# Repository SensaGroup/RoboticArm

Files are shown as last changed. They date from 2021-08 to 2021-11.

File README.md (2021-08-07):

# SENSA - Robotic Arm 

Genral repository for files pertaining to the robotic arm that is part of SENSA GROUP education.  

## Description
The PCB interfaces the microcontroller with 5 stepper drivers and 5 encoders. 

## Features
- Main controller: ESP32WROOM-U.
- Wifi.
- Bluetooth.
- Programming over USB C. 
- 2x TB6600 Drivers. 
- 3x pinouts for general stepstick drivers. 
- 5x AMT102 encoder inputs. 
- Software (TBD)

## Pictures
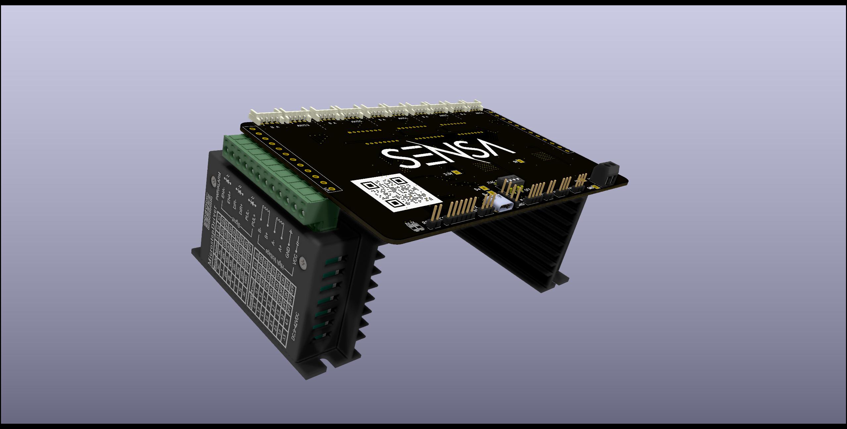
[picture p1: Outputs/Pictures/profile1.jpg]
Top_view


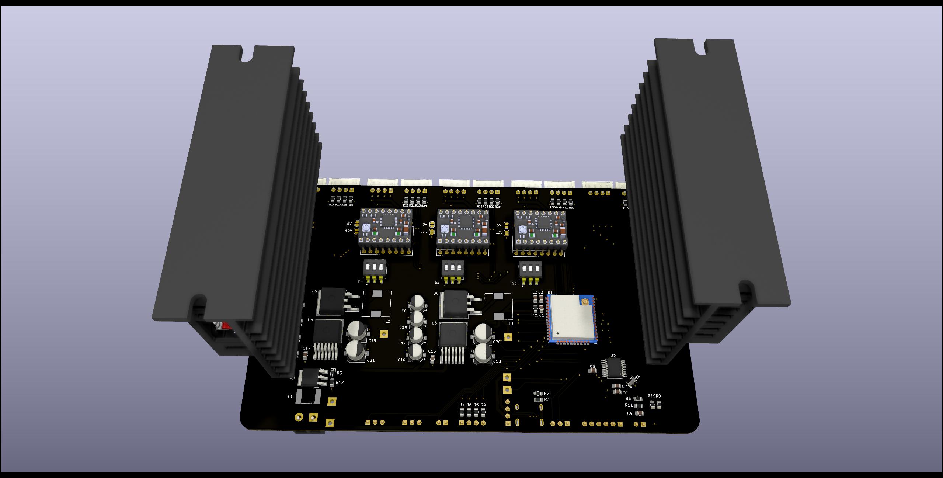
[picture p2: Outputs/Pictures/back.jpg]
Back_view


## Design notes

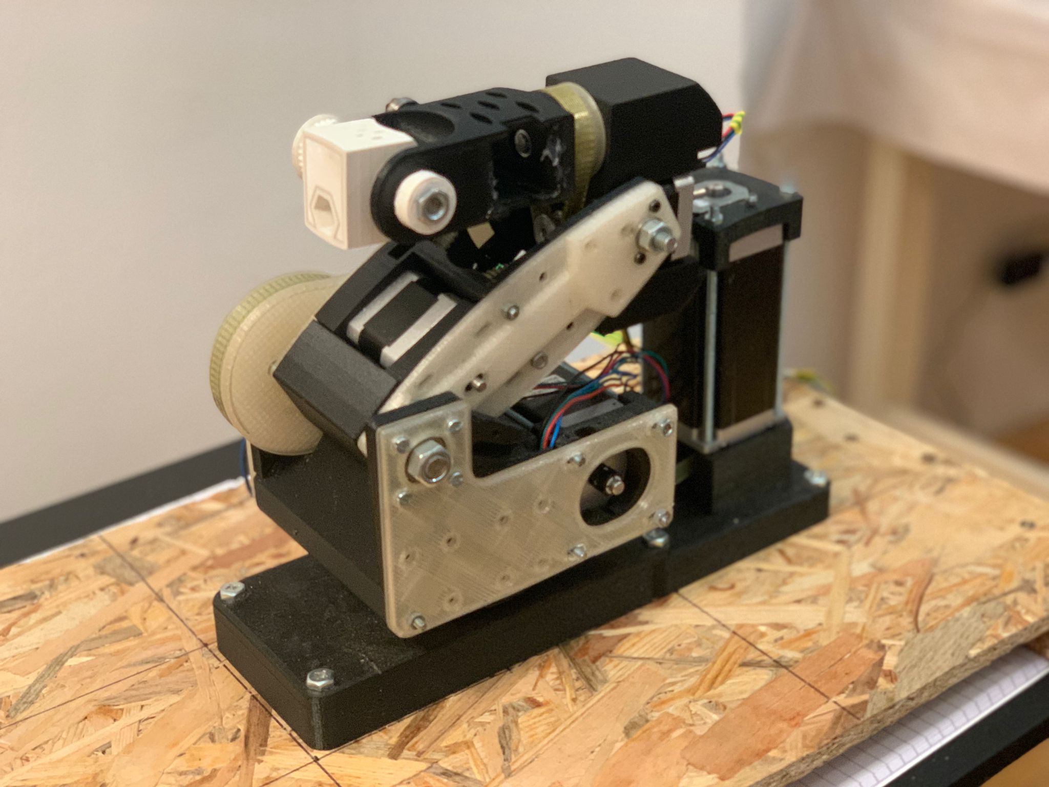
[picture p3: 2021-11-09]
Documents/Slika2.jpeg

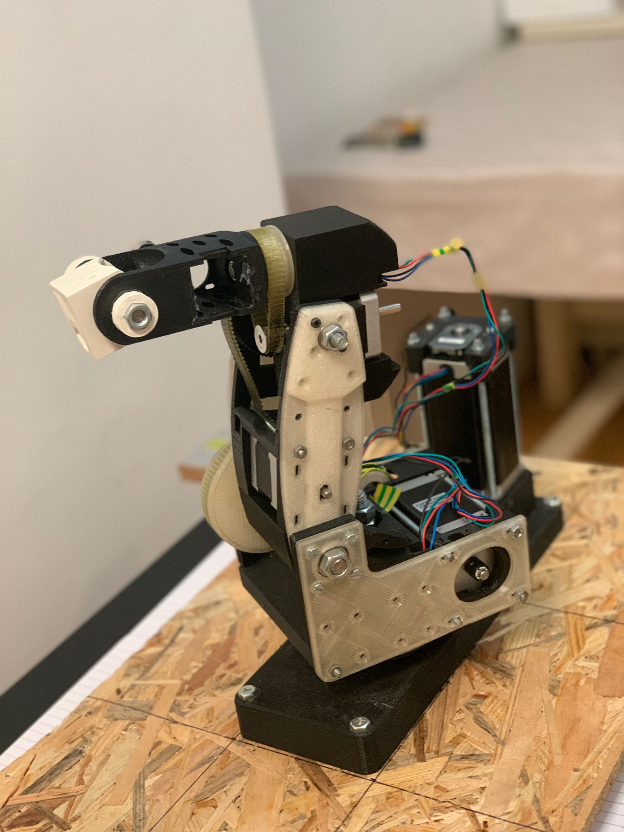
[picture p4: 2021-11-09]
Documents/Slika1.jpeg

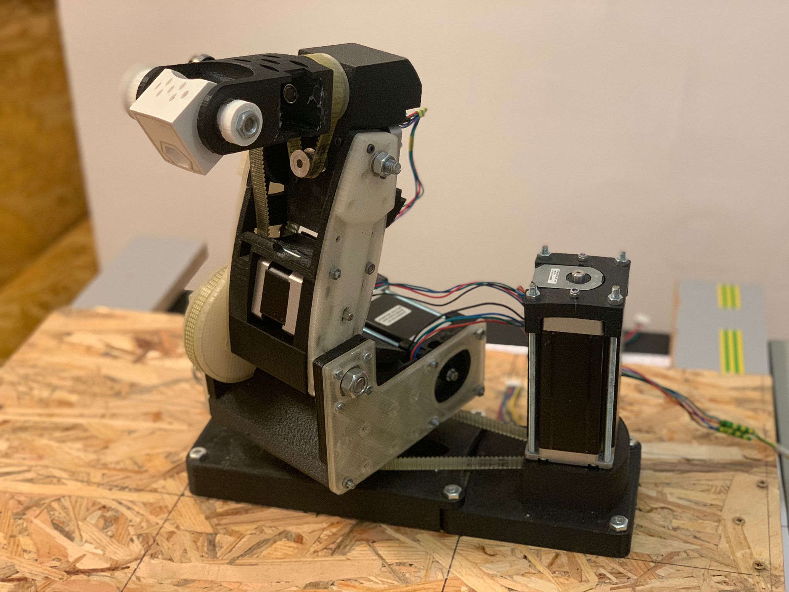
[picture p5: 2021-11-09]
Documents/Slika3.jpeg

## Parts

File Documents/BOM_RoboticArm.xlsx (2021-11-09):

PART | PIECES | PRICE | DISTR. | LINK
ESP32-WROOM-32U (16MB) | 2 | 7.83 | DIGI KEY | https://www.digikey.com/en/products/detail/espressif-systems/ESP32-WROOM-32U-16MB/9381721
AMT102-V | 5 | 100.53 | DIGI KEY | https://www.digikey.com/en/products/detail/cui-devices/AMT102-V/827015
LM2678S-5.0/NOPB | 2 | 11.78 | DIGI KEY | https://www.digikey.com/en/products/detail/texas-instruments/LM2678S-5-0-NOPB/363825
LM2678SX-3.3/NOPB | 2 | 10.95 | DIGI KEY | https://www.digikey.com/en/products/detail/texas-instruments/LM2678SX-3-3-NOPB/366920
ANTX100P011B24003 | 2 | 2.57 | DIGI KEY | https://www.digikey.com/en/products/detail/yageo/ANTX100P011B24003/9360397
ATP106-TL-H | 1 | 0.82 | DIGI KEY | https://www.digikey.com/en/products/detail/on-semiconductor/ATP106-TL-H/2165409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
ASMDC300F/24-2 | 1 | 0.76 | DIGI KEY | https://www.digikey.com/en/products/detail/littelfuse-inc/ASMDC300F-24-2/6623875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
STPS8H100G-TR | 1 | 0.83 | DIGI KEY | https://www.digikey.com/en/products/detail/stmicroelectronics/STPS8H100G-TR/1039718
NP36P06SLG-E1-AY | 1 | 1.26 | DIGI KEY | https://www.digikey.com/en/products/detail/renesas-electronics-america-inc/NP36P06SLG-E1-AY/2764260
ETQ-P4M220KVC | 1 | 0.98 | DIGI KEY | https://www.digikey.com/en/products/detail/panasonic-electronic-components/ETQ-P4M220KVC/6134801
1054500101 | 2 | 3.69 | DIGI KEY | https://www.digikey.com/en/products/detail/molex/1054500101/5843890
MCP2200-I/SS | 2 | 5.94 | FARNELL | https://export.farnell.com/microchip/mcp2200-i-ss/ic-usb2-0-to-uart-w-gpio-20ssop/dp/1781149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
AWSCR-12.00CELB-C33-T3 | 2 | 0.93 | DIGI KEY | https://www.digikey.com/en/products/detail/abracon-llc/AWSCR-12-00CELB-C33-T3/10232536
156120VS75000 | 20 | 3.03 | DIGI KEY | https://www.digikey.com/en/products/detail/w%C3%BCrth-elektronik/156120VS75000/4490062
10081121 | 10 | 14.66 | DIGI KEY | https://www.digikey.com/en/products/detail/molex/0010081121/3072144?s=N4IgTCBcDaIIwAYEA45zHEBdAvkA
S4B-XH-A-1(LF)(SN) | 100 | 15.28 | DIGI KEY | https://www.digikey.com/en/products/detail/jst-sales-america-inc/S4B-XH-A-1-LF-SN/9961923
XHP-4 | 100 | 5.12 | DIGI KEY | https://www.digikey.com/en/products/detail/jst-sales-america-inc/XHP-4/683353
SXH-002T-P0.6 | 500 | 11.62 | DIGI KEY | https://www.digikey.com/en/products/detail/jst-sales-america-inc/SXH-002T-P0-6/1651063
1718560003 | 50 | 13.65 | DIGI KEY | https://www.digikey.com/en/products/detail/molex/1718560003/4423110
DS04-254-2-03BK-SMT | 10 | 4.39 | DIGI KEY | https://www.digikey.com/en/products/detail/cui-devices/DS04-254-2-03BK-SMT/11310920
09200-71-BDGB00 | 50 | 1.6 | DIGI KEY | https://www.digikey.com/en/products/detail/metz-connect-usa-inc/09200-71-BDGB00/13536314
DS04-254-2-04BK-SMT | 10 | 4.95 | DIGI KEY | https://www.digikey.com/en/products/detail/cui-devices/DS04-254-2-04BK-SMT/11310827
 |  |  | SIMPLE:
CRGCQ0805J100R | 100 | 1.47 | DIGI KEY | https://www.digikey.com/en/products/detail/te-connectivity-passive-product/CRGCQ0805J100R/8576730
LMK212BJ106MG-T | 10 | 1.24 | DIGI KEY | https://www.digikey.com/en/products/detail/taiyo-yuden/LMK212BJ106MG-T/1171629
CC0805ZRY5V9BB104 | 10 | 0.59 | DIGI KEY | https://www.digikey.com/en/products/detail/yageo/CC0805ZRY5V9BB104/2103099
C0805C474K5RECAUTO | 10 | 1.56 | DIGI KEY | https://www.digikey.com/en/products/detail/kemet/C0805C474K5RECAUTO/8646710
865080449011 | 10 | 3.95 | DIGI KEY | https://www.digikey.com/en/products/detail/w%C3%BCrth-elektronik/865080449011/5728034
C0805C103K1RAC7210 | 10 | 0.52 | DIGI KEY | https://www.digikey.com/en/products/detail/kemet/C0805C103K1RAC7210/8572452
865080645009 | 10 | 2.61 | DIGI KEY | https://www.digikey.com/en/products/detail/w%C3%BCrth-elektronik/865080645009/5728049
865080442003 | 20 | 3.2 | DIGI KEY | https://www.digikey.com/en/products/detail/w%C3%BCrth-elektronik/865080442003/5728026
ESR10EZPJ102 | 10 | 0.69 | DIGI KEY | https://www.digikey.com/en/products/detail/rohm-semiconductor/ESR10EZPJ102/1762748
RMCF0805JT5K10 | 10 | 0.17 | DIGI KEY | https://www.digikey.com/en/products/detail/stackpole-electronics-inc/RMCF0805JT5K10/1757930
RNCF0805DTE470R | 10 | 0.92 | DIGI KEY | https://www.digikey.com/en/products/detail/stackpole-electronics-inc/RNCF0805DTE470R/6241768
CRCW080510K0FKEAC | 10 | 0.53 | DIGI KEY | https://www.digikey.com/en/products/detail/vishay-dale/CRCW080510K0FKEAC/7928398
RMCF0805FT2K00 | 100 | 0.92 | DIGI KEY | https://www.digikey.com/en/products/detail/stackpole-electronics-inc/RMCF0805FT2K00/1760249
CRCW08053K90FKTA | 20 | 2.13 | DIGI KEY | https://www.digikey.com/en/products/detail/vishay-dale/CRCW08053K90FKTA/1222880
 | TOTAL: | 243.67

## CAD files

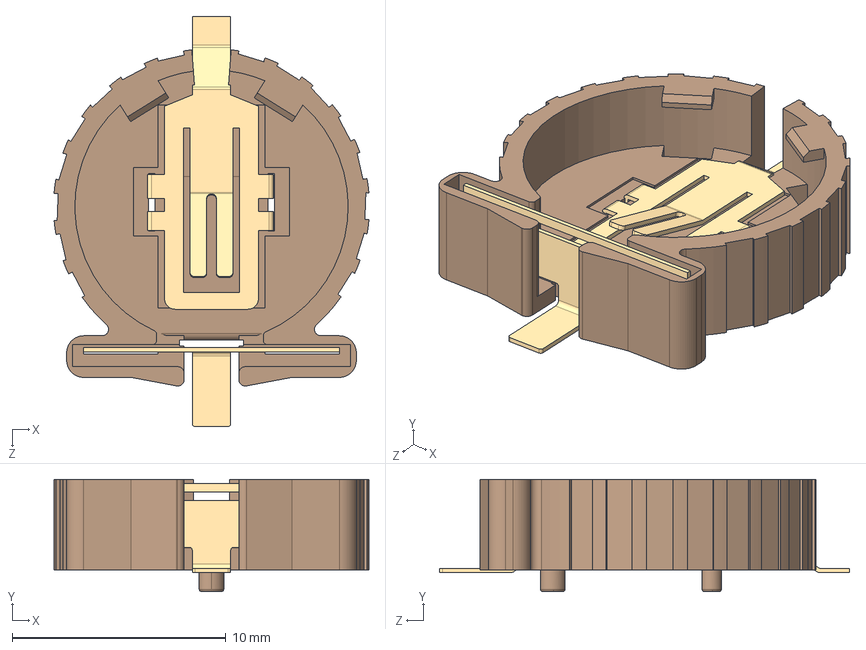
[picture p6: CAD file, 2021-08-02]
Arm_Mainboard/AddOns/3D/User Library-s8411-45r_asm.STEP
14.7 x 5.25 x 19.2 mm
S841-HOLDER
S841-LOWER-CONTACT
S841-REAR-CONTACT

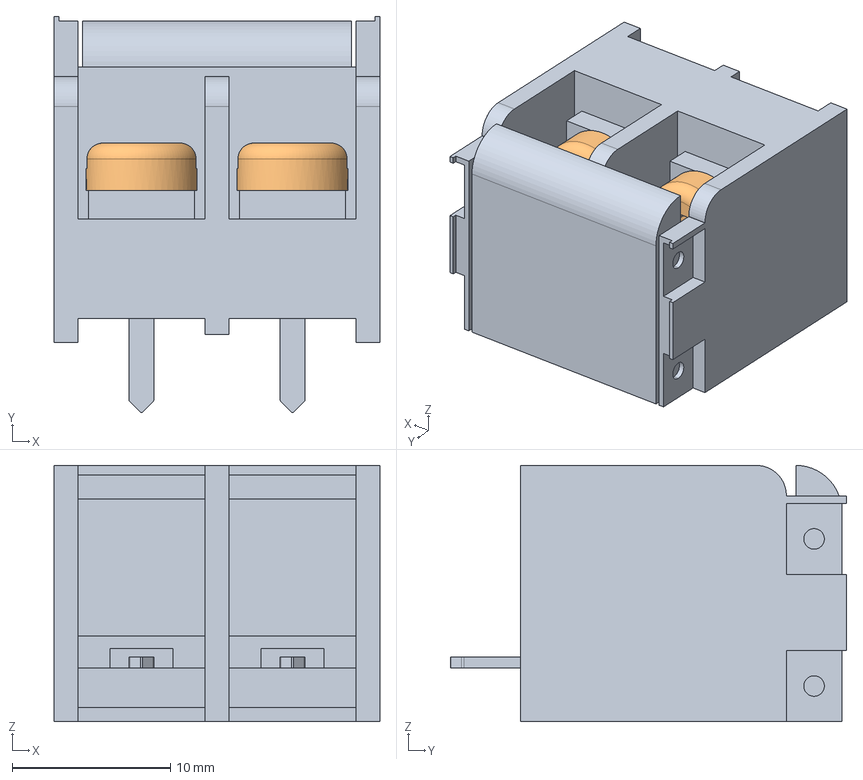
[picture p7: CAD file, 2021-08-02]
Arm_Mainboard/AddOns/3D/hb9500_asm.stp
20.6 x 25.0 x 16.2 mm
HB9500-1
M5X6 x 2

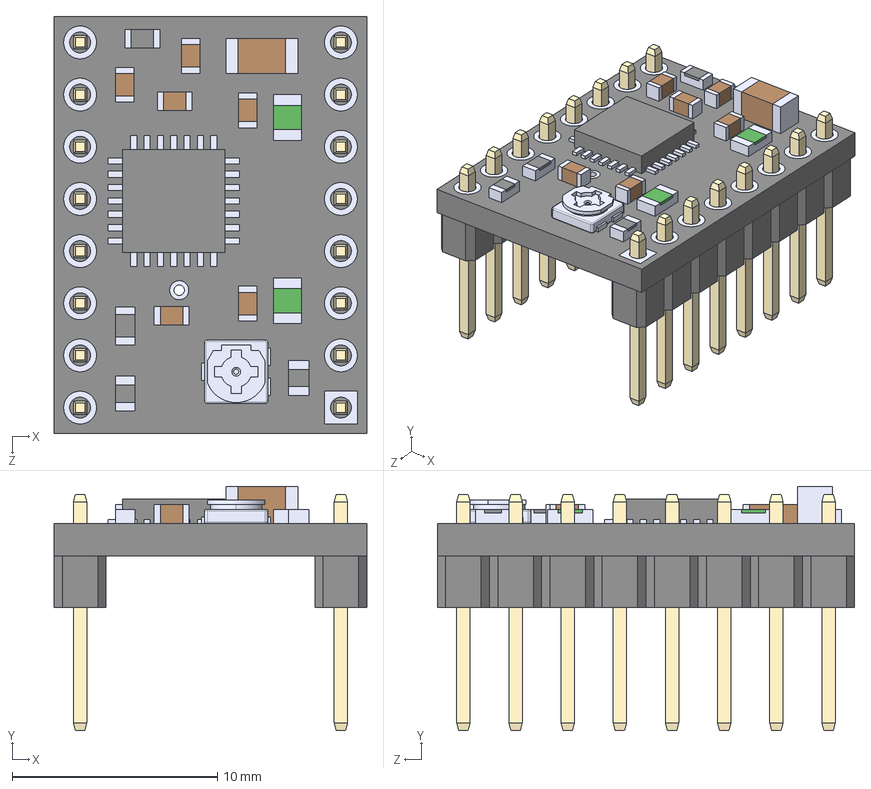
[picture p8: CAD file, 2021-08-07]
Arm_Mainboard/AddOns/3D/A4988 STEPPER MOTOR DRIVER CARRIER--3DModel-STEP-56544.STEP
15.2 x 11.9 x 20.3 mm

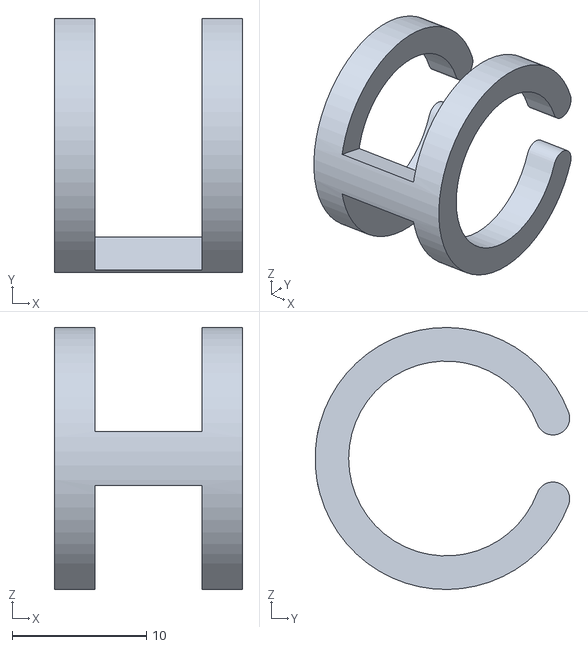
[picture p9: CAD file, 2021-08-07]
For 3D printing/Axis4limit.STL
14.0 x 18.9 x 19.5

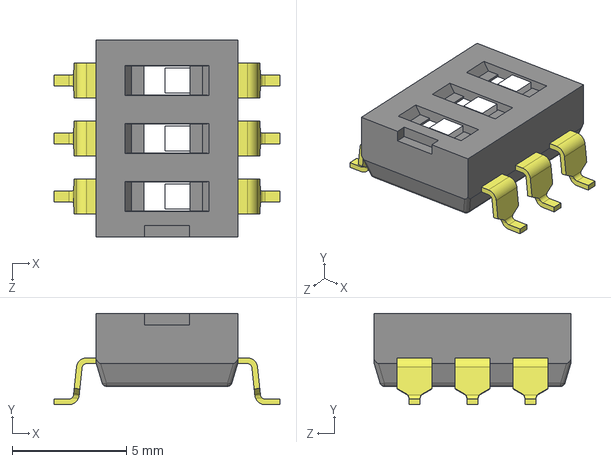
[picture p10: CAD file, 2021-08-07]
Arm_Mainboard/AddOns/3D/CUI_DEVICES_DS04-254-2-03BK-SMT.step
9.90 x 4.00 x 8.62 mm

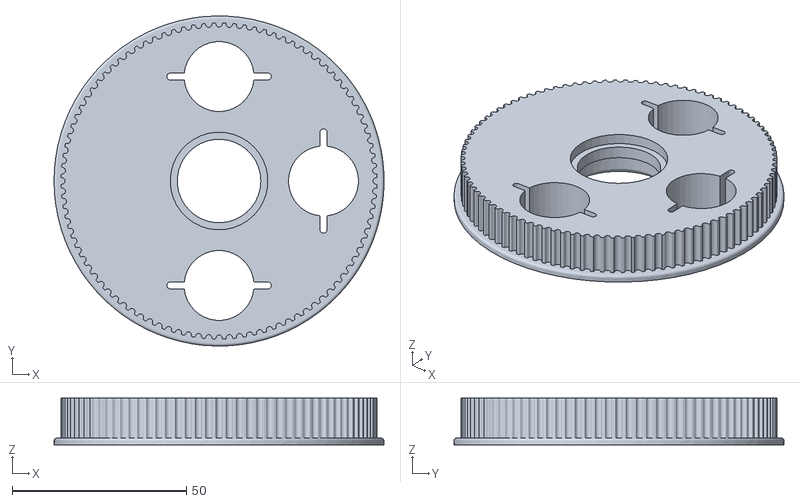
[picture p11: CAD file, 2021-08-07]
For 3D printing/Axis1Pulley_1.STL
94.8 x 94.8 x 13.5

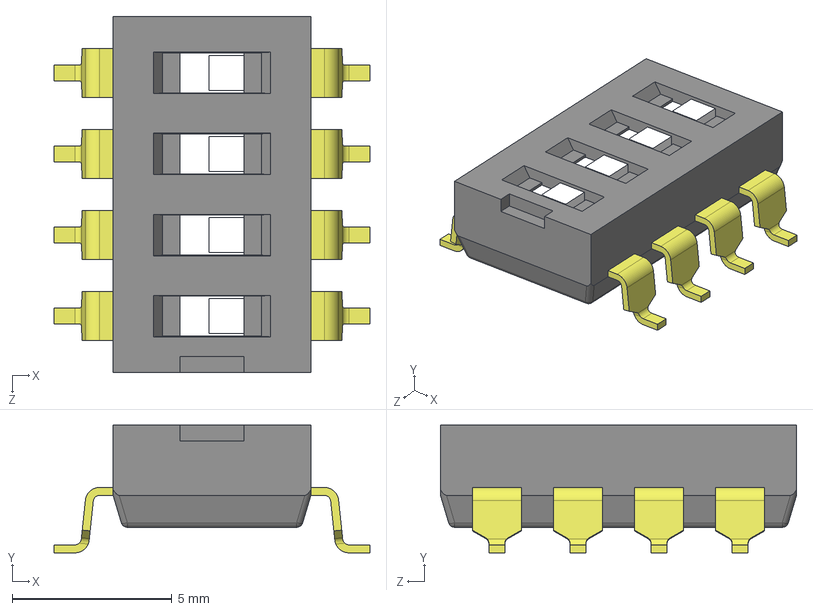
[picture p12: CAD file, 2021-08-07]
Arm_Mainboard/AddOns/3D/CUI_DEVICES_DS04-254-2-04BK-SMT.step
9.90 x 4.00 x 11.2 mm

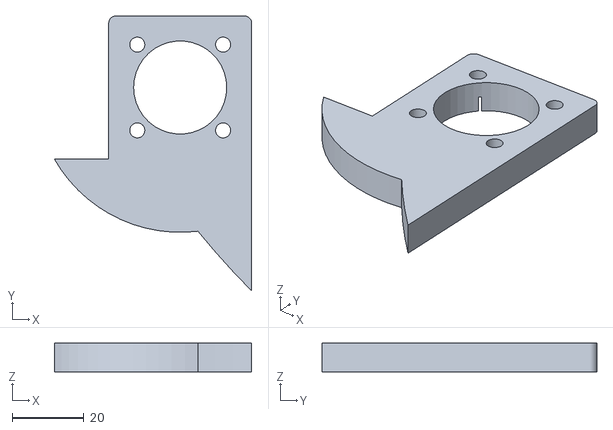
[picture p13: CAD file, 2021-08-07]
For 3D printing/Axis2bearingHolder_1.STL
55.2 x 76.9 x 8.00

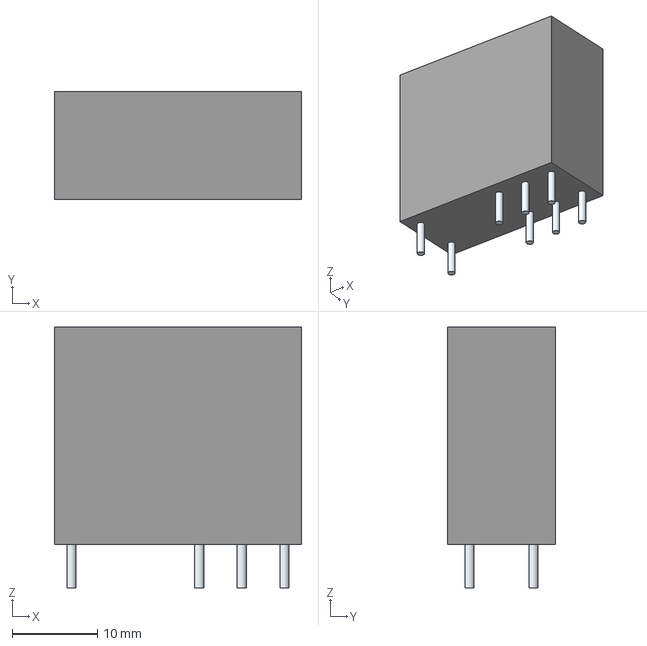
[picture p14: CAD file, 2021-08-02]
Arm_Mainboard/AddOns/3D/G2R-2-DC12.stp
29.0 x 12.7 x 30.6 mm
Leads x 8

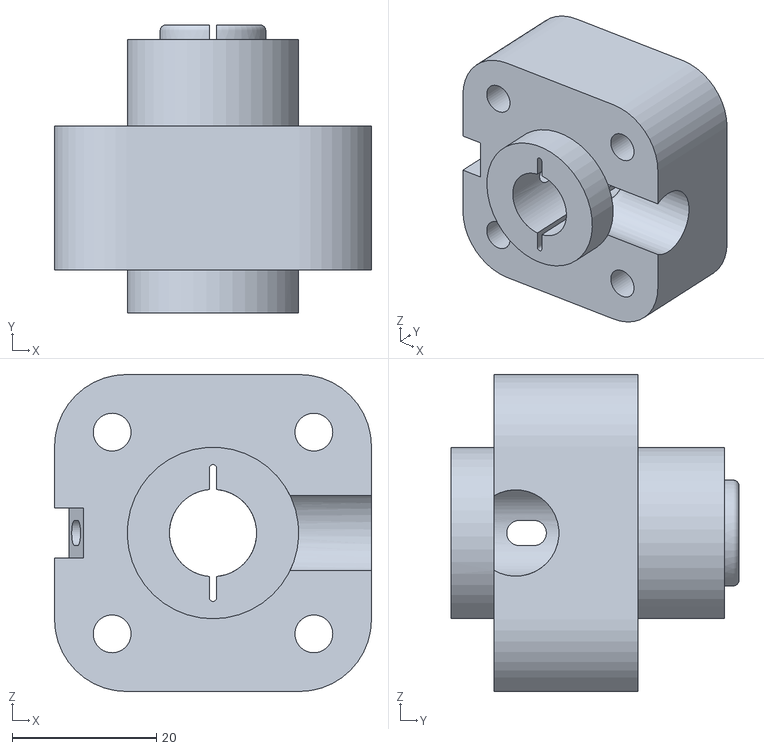
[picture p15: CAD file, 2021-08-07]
For 3D printing/Axis1Holder.STL
44.0 x 40.0 x 44.0

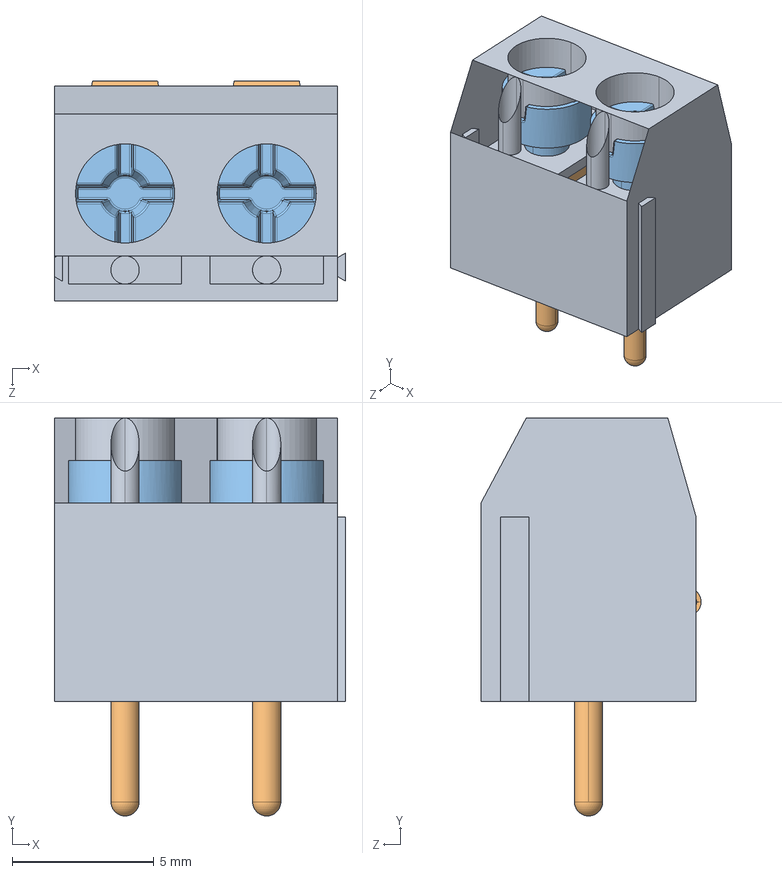
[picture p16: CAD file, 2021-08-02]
Arm_Mainboard/AddOns/3D/2 pins.STEP
10.3 x 14.1 x 7.77 mm
terminal_2 pins
Inner x 2
Screw x 2

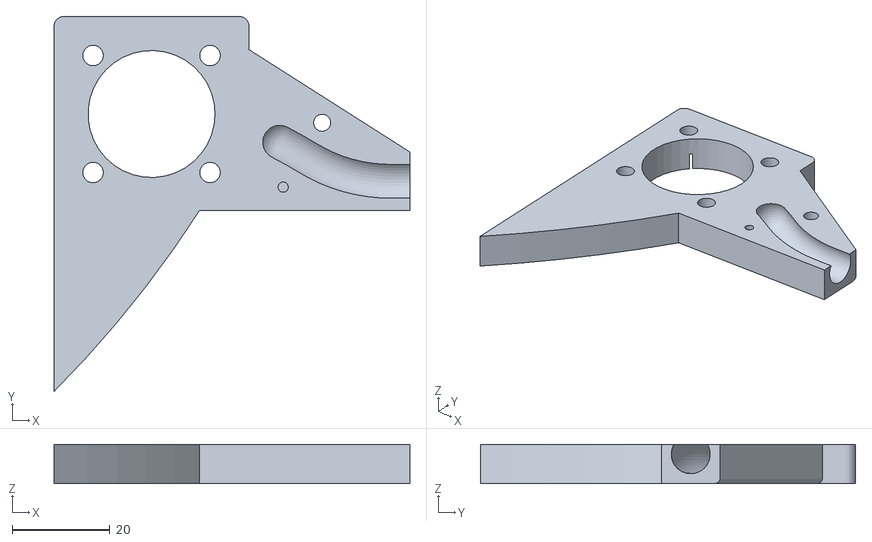
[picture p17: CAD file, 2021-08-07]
For 3D printing/Axis2bearingHolder.STL
73.0 x 76.9 x 8.00

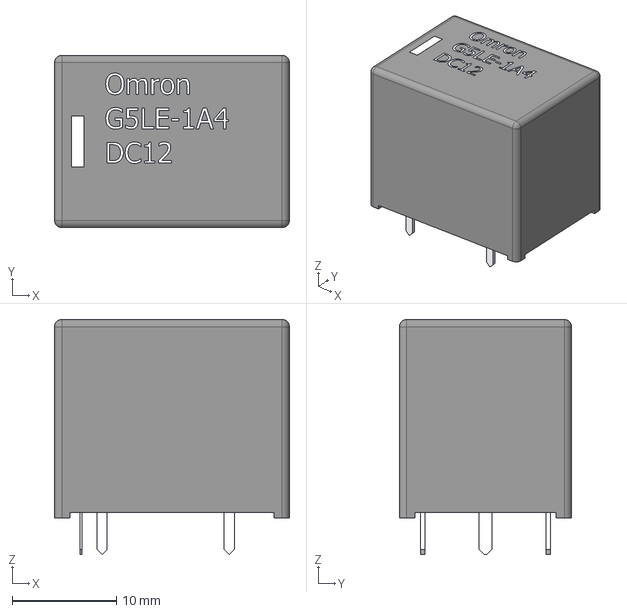
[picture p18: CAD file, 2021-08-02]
Arm_Mainboard/AddOns/3D/Omron_-_G5LE-1A4_DC12.step
22.5 x 16.5 x 22.5 mm

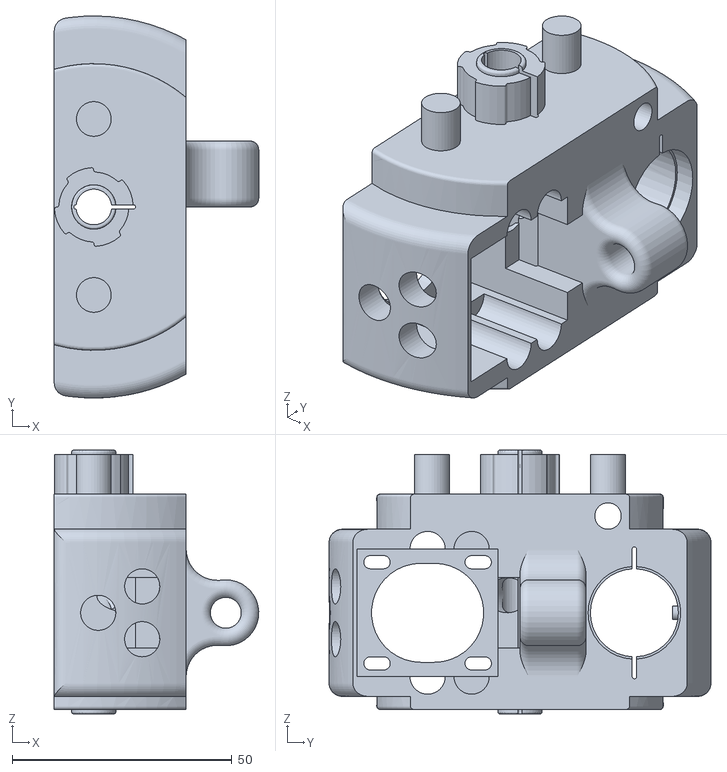
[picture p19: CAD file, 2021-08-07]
For 3D printing/Axis4.STL
46.5 x 86.8 x 60.0

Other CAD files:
Arm_Mainboard/AddOns/3D/MBS6_RCG.stp
For 3D printing/Axis1MotorHolderOp.STL
Arm_Mainboard/AddOns/3D/4 pins.STEP
For 3D printing/Axis3cover2.STL
Arm_Mainboard/AddOns/3D/1 pins.STEP
Arm_Mainboard/AddOns/3D/105450-0101.step
Arm_Mainboard/AddOns/3D/3 pins.STEP
Arm_Mainboard/AddOns/3D/577202B00000G.STEP
Arm_Mainboard/AddOns/3D/74HCT1G04GV,125.stp
Arm_Mainboard/AddOns/3D/AGQ200A24Z.stp
Arm_Mainboard/AddOns/3D/CSD19534Q5AT.STEP
Arm_Mainboard/AddOns/3D/DMP3007SFG-7.stp
Arm_Mainboard/AddOns/3D/S8411-45R--3DModel-STEP-56544.STEP
Arm_Mainboard/AddOns/3D/User Library-TB2.STEP
Arm_Mainboard/AddOns/3D/relay_omron_G5Q.STEP
For 3D printing/Axis1MotorHolder.STL
For 3D printing/Axis1washer.STL
For 3D printing/Axis2MotorOp.STL
For 3D printing/Axis2Pulley_1.STL
For 3D printing/Axis2part2.STL
For 3D printing/Axis3cover1.STL
For 3D printing/Axis3part3.STL
For 3D printing/Axis5.STL
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

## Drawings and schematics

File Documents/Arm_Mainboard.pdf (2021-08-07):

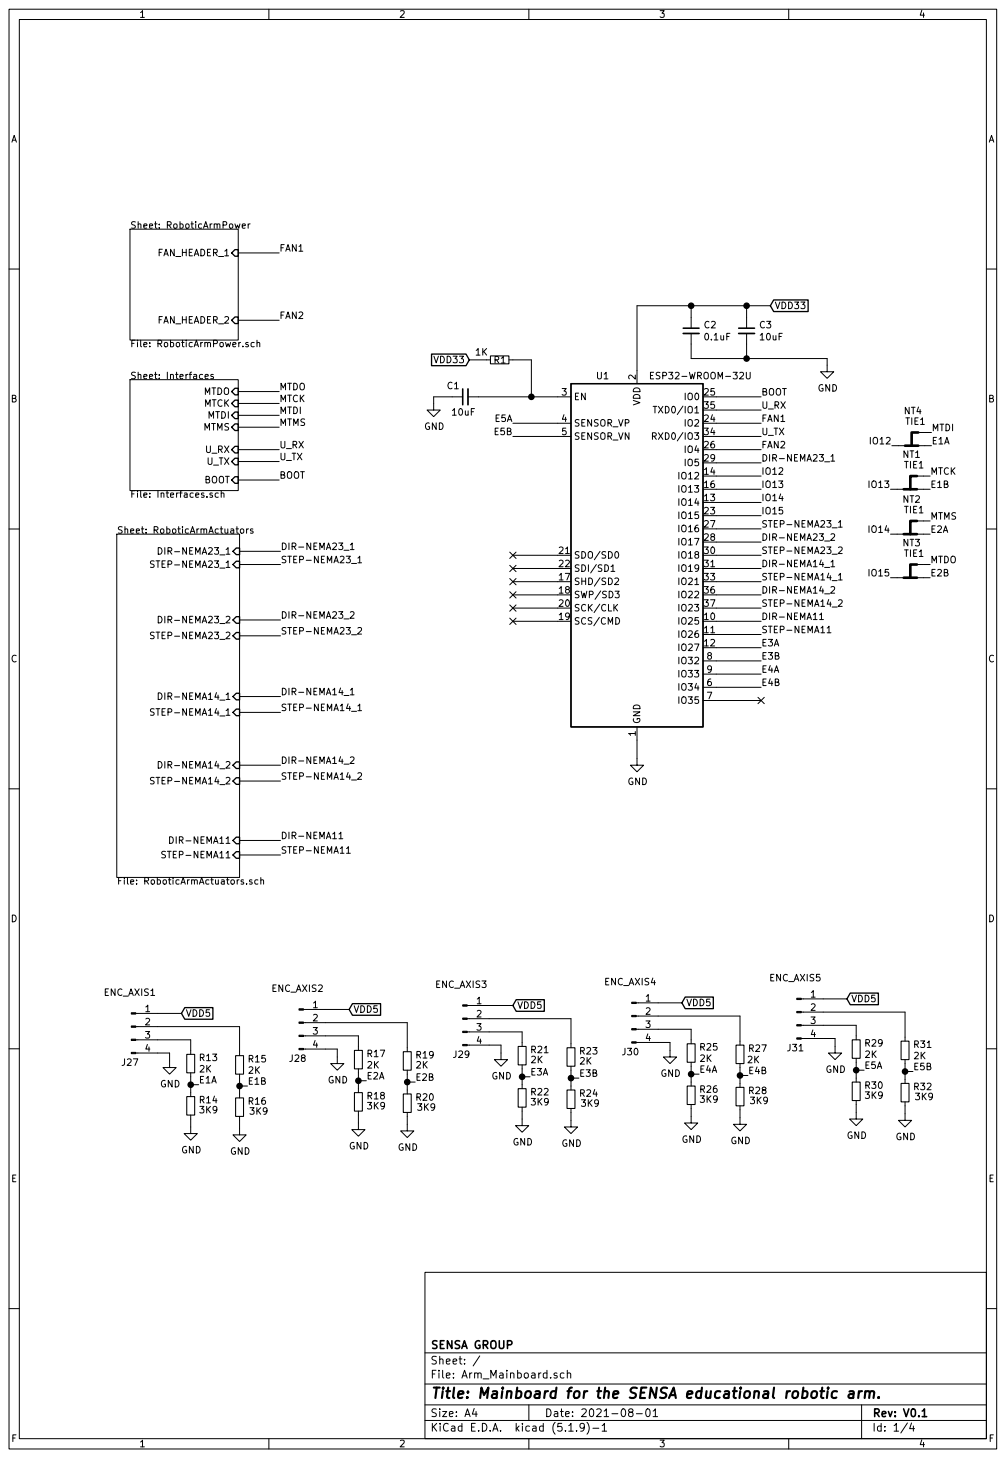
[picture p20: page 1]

Sheet: RoboticArmPower File: RoboticArmPower.sch FAN_HEADER_1 FAN_HEADER_2 Sheet: RoboticArmActuators File: RoboticArmActuators.sch DIR-NEMA23_1 STEP-NEMA23_1 DIR-NEMA23_2 STEP-NEMA23_2 DIR-NEMA14_1 STEP-NEMA14_1 DIR-NEMA14_2 STEP-NEMA14_2 STEP-NEMA11 DIR-NEMA11

Sheet: Interfaces File: Interfaces.schBOOT U_TX U_RX MTMS MTDI MTCK MTDO

2 SCK/CLK 20 SDO/SD0 21 SDI/SD1 22

U_TX MTDO MTMS MTCK MTDI

File: Arm_Mainboard.sch Sheet: / SENSA GROUP

Id: 1/4 Title: Mainboard for the SENSA educational robotic arm.

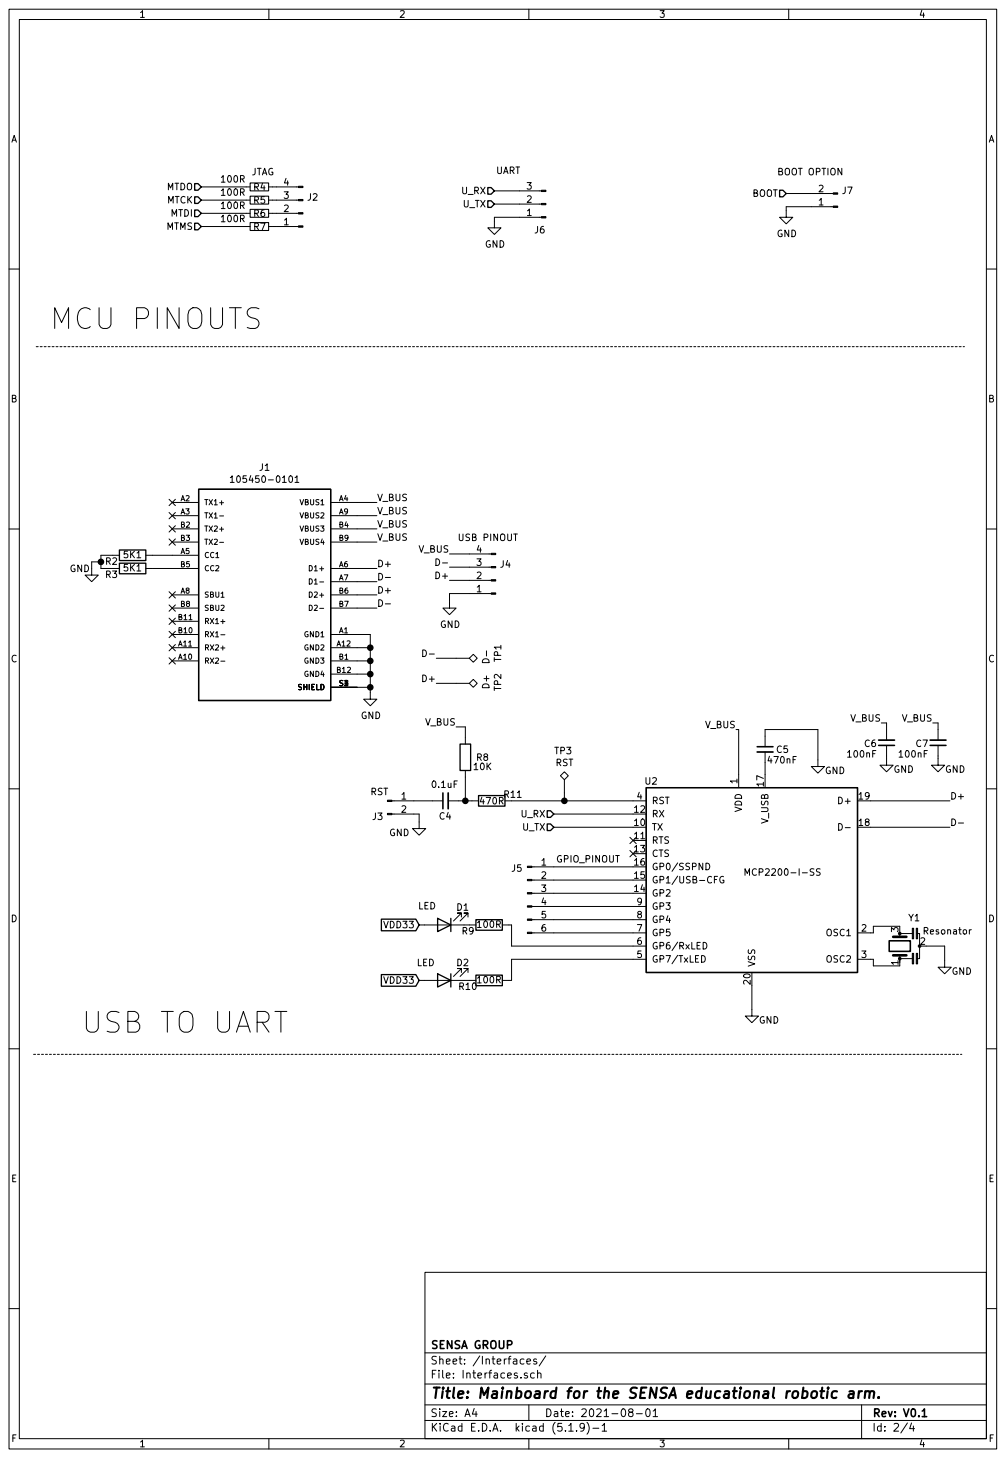
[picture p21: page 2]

1 TX 10 RTS 11 RX 12 CTS 13 GP2 14 GP1/USB-CFG 15 GP0/SSPND 16 V_USB 17 D- 18 D+ 19 OSC1 2 VSS 20 OSC2 3 RST 4 GP7/TxLED 5 GP6/RxLED 6 GP5 7 GP4 8 GP3 9 U2 MCP2200-I-SS

Id: 2/4 Title: Mainboard for the SENSA educational robotic arm. File: Interfaces.sch Sheet: /Interfaces/ SENSA GROUP

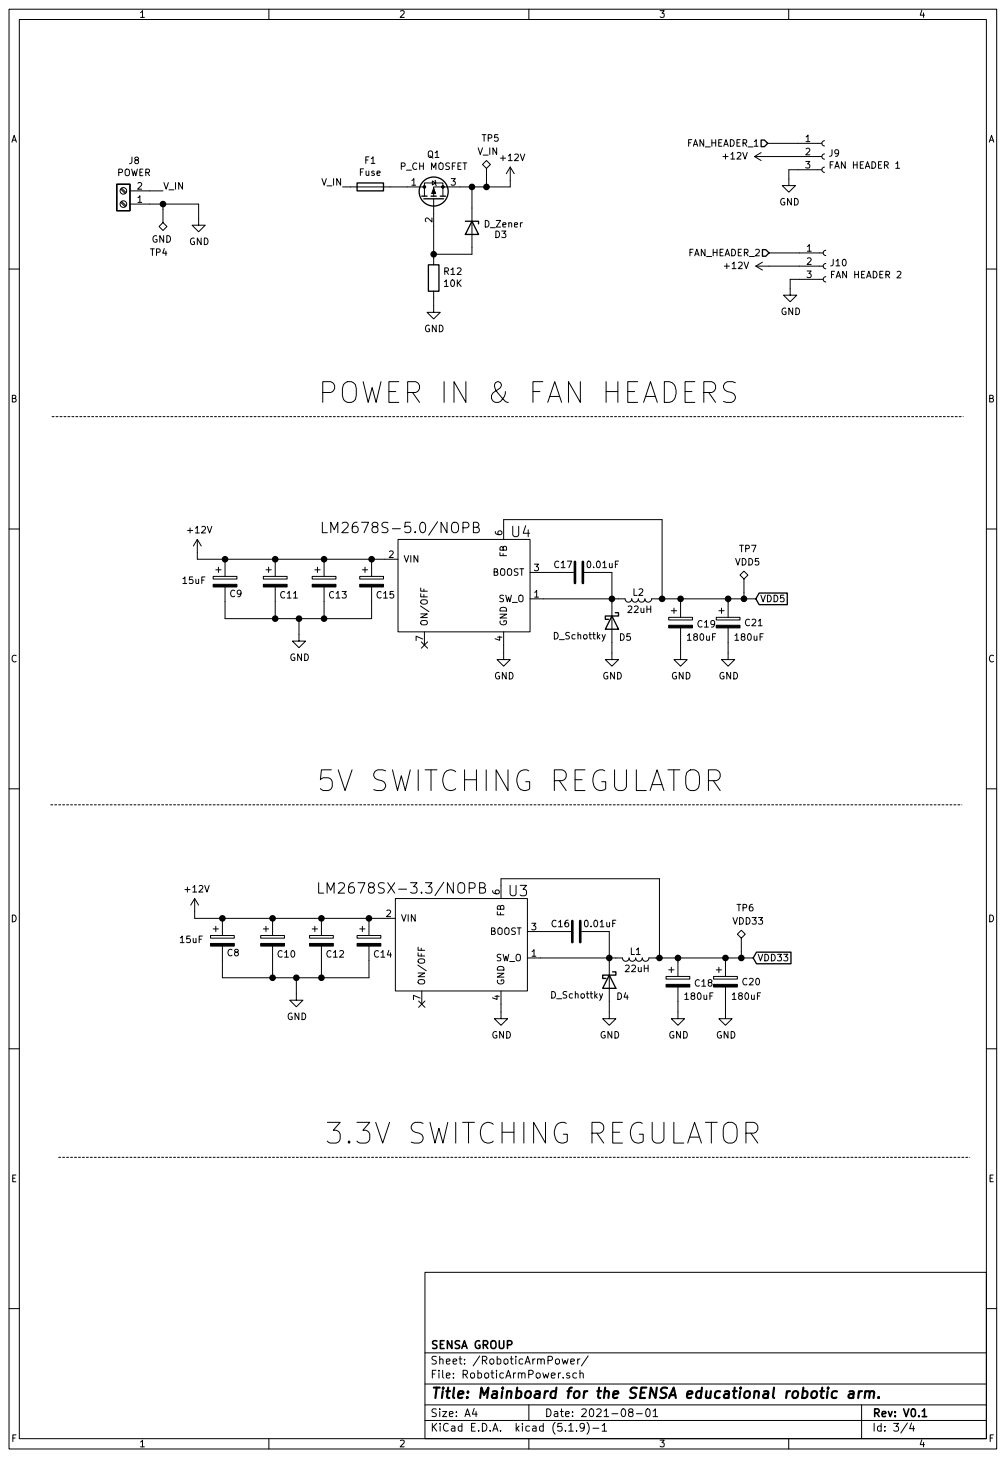
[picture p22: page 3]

POWER IN & FAN HEADERS

Id: 3/4 Title: Mainboard for the SENSA educational robotic arm. File: RoboticArmPower.sch Sheet: /RoboticArmPower/ SENSA GROUP

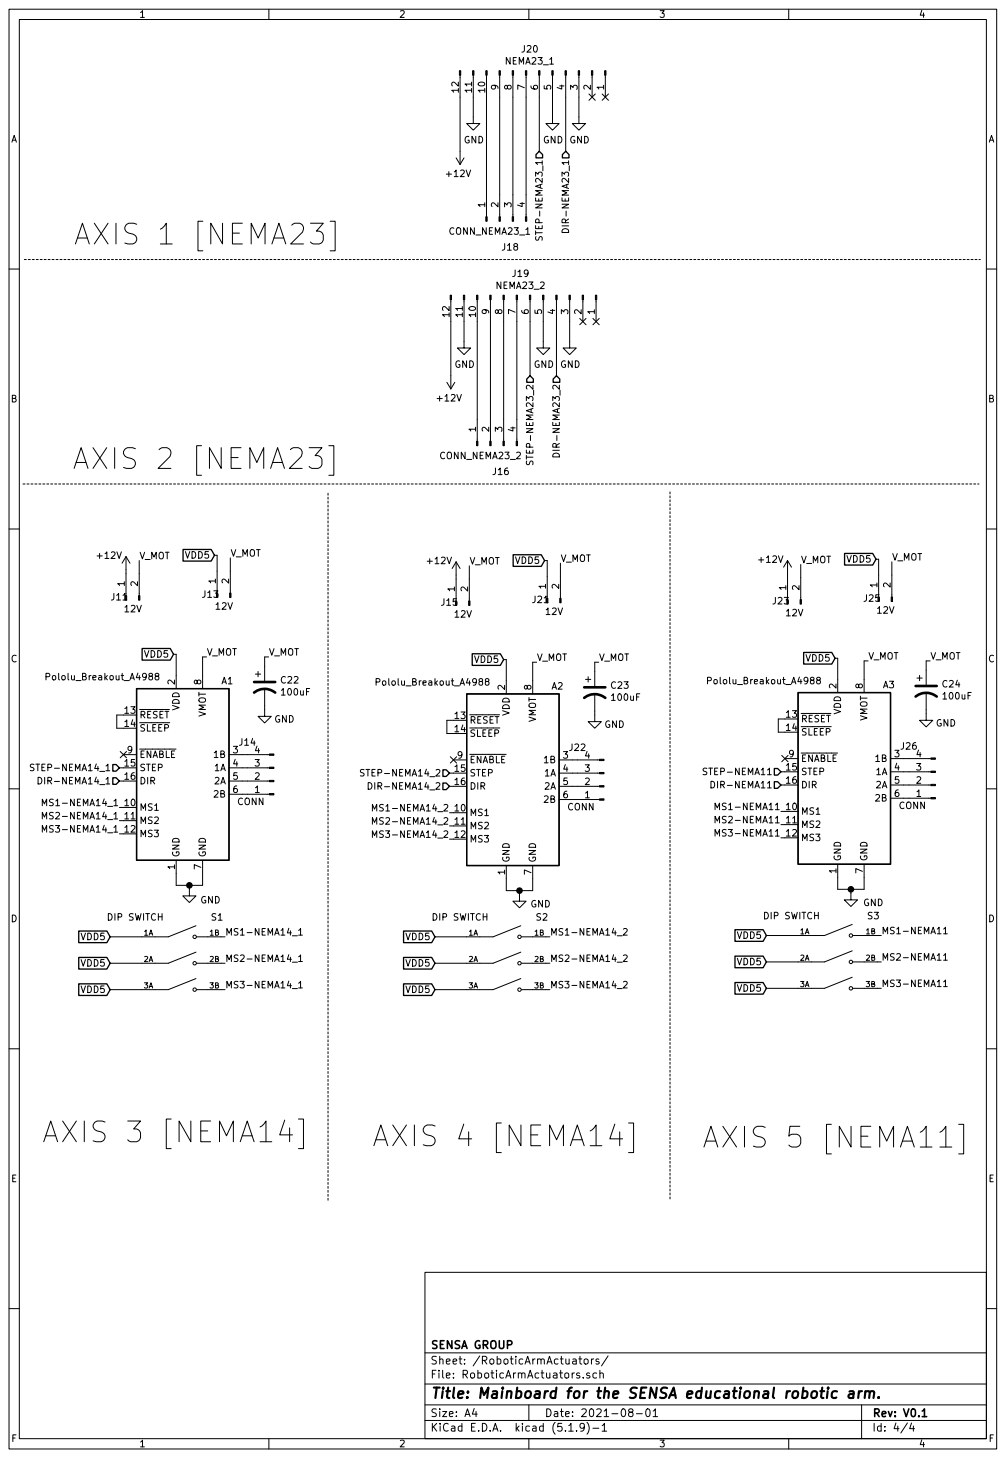
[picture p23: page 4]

1 MS1 10 MS2 11 MS3 12 RESET 13 SLEEP 14 STEP 15 DIR 16 VDD

Id: 4/4 Title: Mainboard for the SENSA educational robotic arm. File: RoboticArmActuators.sch Sheet: /RoboticArmActuators/ SENSA GROUP

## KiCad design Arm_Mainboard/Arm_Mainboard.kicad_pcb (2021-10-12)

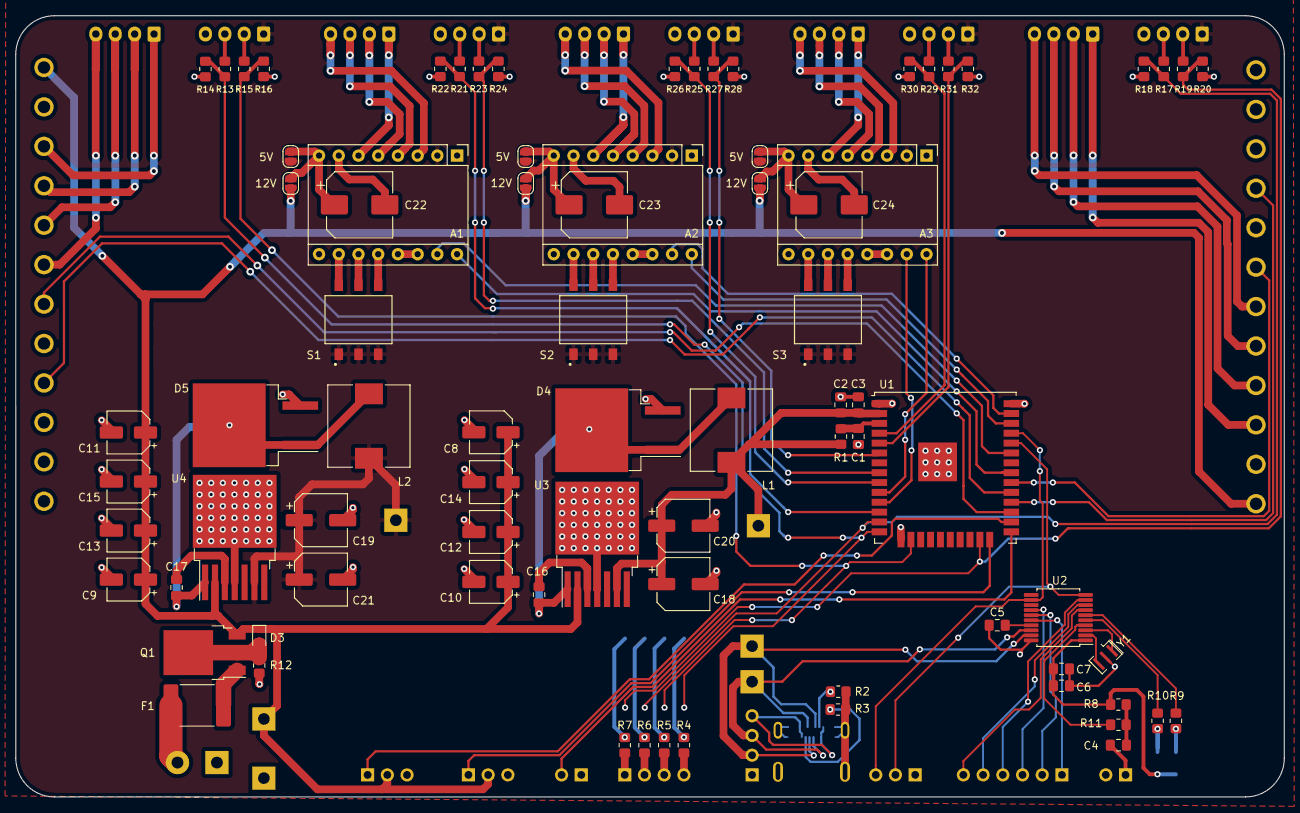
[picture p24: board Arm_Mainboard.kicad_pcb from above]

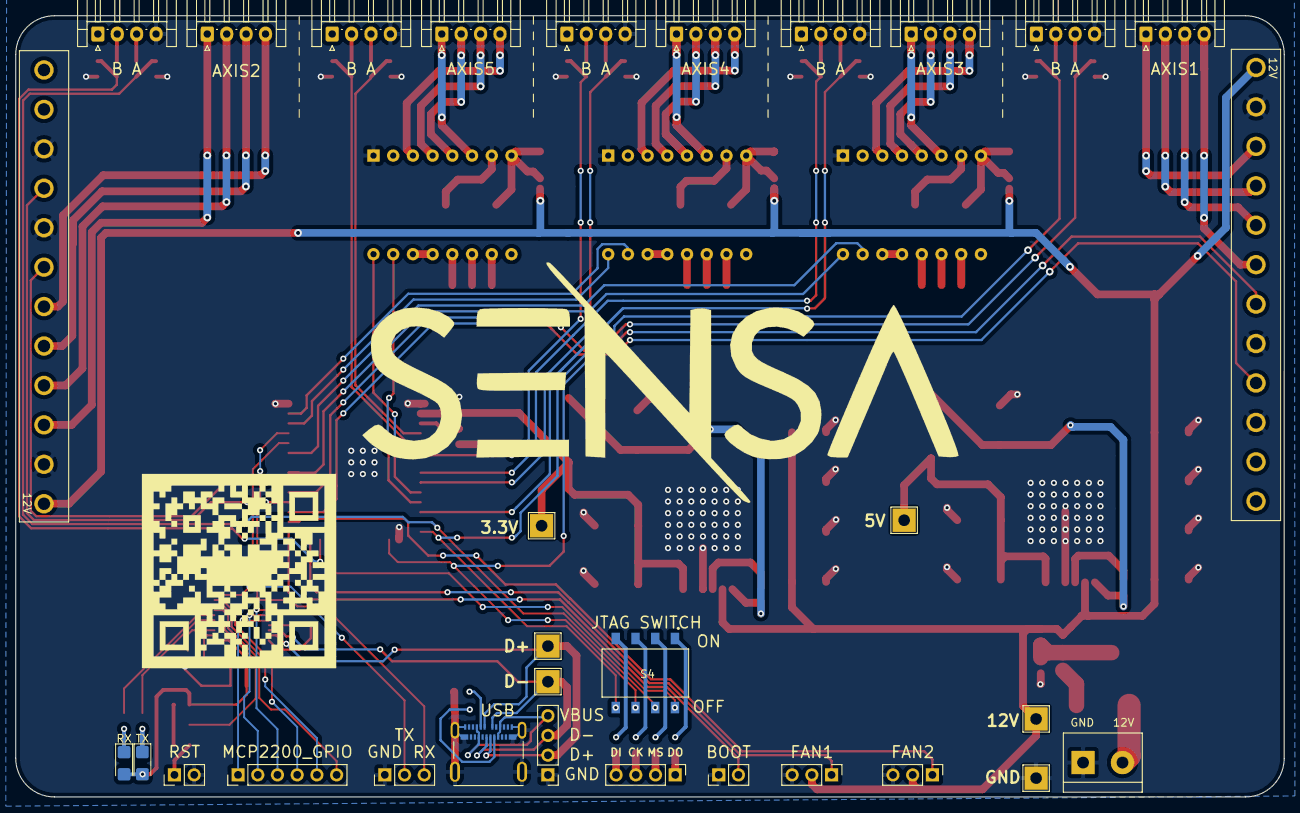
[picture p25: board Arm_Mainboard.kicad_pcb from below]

Board: 2 copper layers, 163.4 x 100.6 mm, 111 parts (31 on the bottom side), 109 nets.

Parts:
3.3V: VDD33; TestPoint_THTPad_3.0x3.0mm_Drill1.5mm
5V, 5V#2, 5V#3, 12V, 12V#2, 12V#3: 12V; SolderJumper-2_P1.3mm_Open_RoundedPad1.0x1.5mm
5V#4: VDD5; TestPoint_THTPad_3.0x3.0mm_Drill1.5mm
12V#4: V_IN; TestPoint_THTPad_3.0x3.0mm_Drill1.5mm
A1, A2, A3: Pololu_Breakout_A4988; Pololu_Breakout-16_15.2x20.3mm
AXIS1: CONN_NEMA23_1; JST_EH_S4B-EH_1x04_P2.50mm_Horizontal
C1, C3: 10uF; C_0805_2012Metric_Pad1.18x1.45mm_HandSolder
C2, C4: 0.1uF; C_0805_2012Metric_Pad1.18x1.45mm_HandSolder
C5: 470nF; C_0805_2012Metric_Pad1.18x1.45mm_HandSolder
C6, C7: 100nF; C_0805_2012Metric_Pad1.18x1.45mm_HandSolder
C8, C9: 15uF; CP_Elec_5x5.3
C10, C11, C12, C13, C14, C15: CP; CP_Elec_5x5.3
C16, C17: 0.01uF; C_0805_2012Metric_Pad1.18x1.45mm_HandSolder
C18, C19, C20, C21: 180uF; CP_Elec_6.3x5.9
C22, C23, C24: 100uF; CP_Elec_8x10
D3: D_Zener; D_SOD-323
D4, D5: D_Schottky; TO-263-2_TabPin1
D+: D+; TestPoint_THTPad_3.0x3.0mm_Drill1.5mm
D-: D-; TestPoint_THTPad_3.0x3.0mm_Drill1.5mm
F1: Fuse; Fuse_2920_7451Metric
GND: GND; TestPoint_THTPad_3.0x3.0mm_Drill1.5mm
J2: JTAG; PinHeader_1x04_P2.54mm_Vertical
J4: USB PINOUT; PinHeader_1x04_P2.54mm_Vertical
J6: UART; PinHeader_1x03_P2.54mm_Vertical
J7: BOOT OPTION; PinHeader_1x02_P2.54mm_Vertical
J8: POWER; TerminalBlock_bornier-2_P5.08mmCOPY
J9: FAN HEADER 1; PinHeader_1x03_P2.54mm_Vertical
J10: FAN HEADER 2; PinHeader_1x03_P2.54mm_Vertical
J14, J22, J26: CONN; JST_EH_S4B-EH_1x04_P2.50mm_Horizontal
J16: CONN_NEMA23_2; JST_EH_S4B-EH_1x04_P2.50mm_Horizontal
J19: NEMA23_2; Molex_12PIN
J20: NEMA23_1; Molex_12PIN
J27: ENC_AXIS1; JST_EH_S4B-EH_1x04_P2.50mm_Horizontal
J28: ENC_AXIS2; JST_EH_S4B-EH_1x04_P2.50mm_Horizontal
J29: ENC_AXIS3; JST_EH_S4B-EH_1x04_P2.50mm_Horizontal
J30: ENC_AXIS4; JST_EH_S4B-EH_1x04_P2.50mm_Horizontal
J31: ENC_AXIS5; JST_EH_S4B-EH_1x04_P2.50mm_Horizontal
L1, L2: 22uH; L_10.4x10.4_H4.8
MCP2200_GPIO: GPIO_PINOUT; PinHeader_1x06_P2.54mm_Vertical
Q1: P_CH MOSFET; TO-252-3_TabPin2
R1: 1K; R_0805_2012Metric_Pad1.20x1.40mm_HandSolder
R2, R3: 5K1; R_0805_2012Metric_Pad1.20x1.40mm_HandSolder
R4, R5, R6, R7, R9, R10: 100R; R_0805_2012Metric_Pad1.20x1.40mm_HandSolder
R8, R12: 10K; R_0805_2012Metric_Pad1.20x1.40mm_HandSolder
R11: 470R; R_0805_2012Metric_Pad1.20x1.40mm_HandSolder
R13, R15, R17, R19, R21, R23, R25, R27, R29, R31: 2K; R_0805_2012Metric_Pad1.20x1.40mm_HandSolder
R14, R16, R18, R20, R22, R24, R26, R28, R30, R32: 3K9; R_0805_2012Metric_Pad1.20x1.40mm_HandSolder
RST: RST; PinHeader_1x02_P2.54mm_Vertical
RX: LED; D_1206_3216Metric_Castellated
S1, S2, S3: DIP SWITCH; SW_DS04-254-2-03BK-SMT
S4: JTAG SELECTOR; SW_DS04-254-2-04BK-SMT
TX: LED; D_1206_3216Metric_Castellated
U1: ESP32-WROOM-32U
U2: MCP2200-I-SS; SSOP-20_5.3x7.2mm_P0.65mm
U3: LM2678SX-3.3/NOPB; TO-263-7_TabPin4
U4: LM2678S-5.0/NOPB; TO-263-7_TabPin4
USB : 105450-0101; MOLEX_105450-0101
Y1: Resonator; Resonator_SMD_muRata_CSTxExxV-3Pin_3.0x1.1mm

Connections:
+12V: 12V.1, 12V#2.1, 12V#3.1, 12V#4.1, C8.1, C9.1, C10.1, C11.1, C12.1, C13.1, C14.1, C15.1, D3.1, J9.2, J10.2, J19.12, J20.12, Q1.3, U3.2, U4.2
/BOOT: J7.2, U1.25
/DIR-NEMA11: A3.16, U1.10
/DIR-NEMA14_1: A1.16, U1.31
/DIR-NEMA14_2: A2.16, U1.36
/DIR-NEMA23_1: J20.4, U1.29
/DIR-NEMA23_2: J19.4, U1.28
/E1A: R13.2, R14.1, S4.4B, U1.14
/E1B: R15.2, R16.1, S4.3B, U1.16
/E2A: R17.2, R18.1, S4.2B, U1.13
/E2B: R19.2, R20.1, S4.1B, U1.23
/E3A: R21.2, R22.1, U1.12
/E3B: R23.2, R24.1, U1.8
/E4A: R25.2, R26.1, U1.9
/E4B: R27.2, R28.1, U1.6
/E5A: R29.2, R30.1, U1.4
/E5B: R31.2, R32.1, U1.5
/FAN1: J9.1, U1.24
/FAN2: J10.1, U1.26
/Interfaces/D+: D+.1, J4.2, U2.19, USB.A6, USB.B6
/Interfaces/D-: D-.1, J4.3, U2.18, USB.A7, USB.B7
/Interfaces/V_BUS: C6.2, C7.2, J4.4, R8.1, RX.2, TX.2, U2.1, USB.A4, USB.A9, USB.B4, USB.B9
/MTCK: R5.2, S4.3A
/MTDI: R4.2, S4.4A
/MTDO: R7.2, S4.1A
/MTMS: R6.2, S4.2A
/RoboticArmActuators/MS1-NEMA11: A3.10, S3.1B
/RoboticArmActuators/MS1-NEMA14_1: A1.10, S1.1B
/RoboticArmActuators/MS1-NEMA14_2: A2.10, S2.1B
/RoboticArmActuators/MS2-NEMA11: A3.11, S3.2B
/RoboticArmActuators/MS2-NEMA14_1: A1.11, S1.2B
/RoboticArmActuators/MS2-NEMA14_2: A2.11, S2.2B
/RoboticArmActuators/MS3-NEMA11: A3.12, S3.3B
/RoboticArmActuators/MS3-NEMA14_1: A1.12, S1.3B
/RoboticArmActuators/MS3-NEMA14_2: A2.12, S2.3B
/RoboticArmActuators/V_MOT: 5V.2, 5V#2.2, 5V#3.2, 12V.2, 12V#2.2, 12V#3.2, A1.8, A2.8, A3.8, C22.1, C23.1, C24.1
/RoboticArmPower/V_IN: F1.1, J8.2
/STEP-NEMA11: A3.15, U1.11
/STEP-NEMA14_1: A1.15, U1.33
/STEP-NEMA14_2: A2.15, U1.37
/STEP-NEMA23_1: J20.6, U1.27
/STEP-NEMA23_2: J19.6, U1.30
/U_RX: J6.3, U1.35, U2.12
/U_TX: J6.2, U1.34, U2.10
GND: A1.1, A1.7, A2.1, A2.7, A3.1, A3.7, C1.1, C2.2, C3.2, C5.1, C6.1, C7.1, C8.2, C9.2, C10.2, C11.2, C12.2, C13.2, C14.2, C15.2, C18.2, C19.2, C20.2, C21.2, C22.2, C23.2, C24.2, D4.2, D5.2, GND.1, J4.1, J6.1, J7.1, J8.1, J9.3, J10.3, J19.3, J19.5, J19.11, J20.3, J20.5, J20.11, J27.4, J28.4, J29.4, J30.4, J31.4, R2.1, R3.1, R12.1, R14.2, R16.2, R18.2, R20.2, R22.2, R24.2, R26.2, R28.2, R30.2, R32.2, RST.2, U1.1, U1.15, U1.38, U1.39, U2.20, U3.4, U4.4, USB.A1, USB.A12, USB.B1, USB.B12, USB.S1, USB.S2, USB.S3, USB.S4, Y1.2
unnamed: A1.3, J14.4
unnamed: A1.4, J14.3
unnamed: A1.5, J14.2
unnamed: A1.6, J14.1
unnamed: A1.13, A1.14
unnamed: A2.3, J22.4
unnamed: A2.4, J22.3
unnamed: A2.5, J22.2
unnamed: A2.6, J22.1
unnamed: A2.13, A2.14
unnamed: A3.3, J26.4
unnamed: A3.4, J26.3
unnamed: A3.5, J26.2
unnamed: A3.6, J26.1
unnamed: A3.13, A3.14
unnamed: C1.2, R1.1, U1.3
unnamed: C4.1, RST.1
unnamed: C4.2, R8.2, R11.2
unnamed: C5.2, U2.17
unnamed: C16.1, D4.1, L1.2, U3.1
unnamed: C16.2, U3.3
unnamed: C17.1, D5.1, L2.2, U4.1
unnamed: C17.2, U4.3
unnamed: R9.1, RX.1
unnamed: R10.1, TX.1
unnamed: D3.2, Q1.2, R12.2
unnamed: F1.2, Q1.1
unnamed: R2.2, USB.A5
unnamed: R3.2, USB.B5
unnamed: J2.1, R7.1
unnamed: J2.2, R6.1
unnamed: J2.3, R5.1
unnamed: J2.4, R4.1
unnamed: MCP2200_GPIO.1, U2.16
unnamed: MCP2200_GPIO.2, U2.15
unnamed: MCP2200_GPIO.3, U2.14
unnamed: MCP2200_GPIO.4, U2.9
unnamed: MCP2200_GPIO.5, U2.8
unnamed: MCP2200_GPIO.6, U2.7
unnamed: J16.1, J19.10
unnamed: J16.2, J19.9
unnamed: J16.3, J19.8
unnamed: J16.4, J19.7
unnamed: AXIS1.1, J20.10
unnamed: AXIS1.2, J20.9
unnamed: AXIS1.3, J20.8
unnamed: AXIS1.4, J20.7
unnamed: J27.2, R15.1
unnamed: J27.3, R13.1
unnamed: J28.2, R19.1
unnamed: J28.3, R17.1
unnamed: J29.2, R23.1
unnamed: J29.3, R21.1
unnamed: J30.2, R27.1
unnamed: J30.3, R25.1
unnamed: J31.2, R31.1
unnamed: J31.3, R29.1
unnamed: R9.2, U2.6
unnamed: R10.2, U2.5
unnamed: R11.1, U2.4
unnamed: U2.2, Y1.3
unnamed: U2.3, Y1.1
VDD5: 5V.1, 5V#2.1, 5V#3.1, 5V#4.1, A1.2, A2.2, A3.2, C19.1, C21.1, J27.1, J28.1, J29.1, J30.1, J31.1, L2.1, S1.1A, S1.2A, S1.3A, S2.1A, S2.2A, S2.3A, S3.1A, S3.2A, S3.3A, U4.6
VDD33: 3.3V.1, C2.1, C3.1, C18.1, C20.1, L1.1, R1.2, U1.2, U3.6

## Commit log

2021-08-02 Started schematic
    [1 pins.STEP, 105450-0101.step, 2 pins.STEP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]
2021-11-09 Update with pictures
    [BOM_RoboticArm.xlsx]
